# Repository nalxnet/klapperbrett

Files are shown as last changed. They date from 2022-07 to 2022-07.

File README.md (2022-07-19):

# klapperbrett

Die Klappenanzeige (Salzkotten EC2000-FP6) stammt aus einer Zapfsäule und zeigte die üblichen Werte (Literpreis, Gesamtmenge, Gesamtpreis) an.

Es sind drei Anschlüsse vorhanden:
* Pfostenstecker 10-polig, von außen zugänglich: vmtl. Anschluss an den Rest der Zapfsäule, inkl. Stromversorgung (2 Pins +24V, 2 Pins GND).
* Pfostenstecker 12-polig(?), nur von innen zugänglich: vmtl. Service-Anschluss zur Neuprogrammierung, kein +24V oder +5V, nur GND.
* 2 Bohrungen für +24V und GND, nicht verlötet.

Steuerung erfolgt original über einen 8-bit Mikrocontroller, der in einen 40-pol. IC-Sockel gesteckt ist. Hier setzen wir an und ersetzen diesen mit einem Arduino/ESP.

Es gibt 3 Zeilen, die oberen beiden haben 5 Elemente, die unterste hat 4. Jedes Element hat 7 Segmente zur Anzeige einer Zahl. Logisch sind zur Ansteuerung alle Elemente in einer Reihe aufgebaut, dadurch lassen sich die einzelnen Segmente als Matrix darstellen, wobei die Elemente die Spalten und die Segmente die Zeilen darstellen. Jedes Segment besteht aus einem Elektromagneten, der je nach Stromfluss anders polarisiert ist und dadurch das Segment in An- bzw. Aus-Position bewegt. Dafür ist eine Seite der Spule direkt an die Spaltenleitung angeschlossen. Die andere Seite der Spule ist mit jeweils einer Diode an zwei Elementleitungen angeschlossen. Eine zum Bewegen in An-Position, die andere für die Aus-Position.

Die Ansteuerung der einzelnen Segmente übernehmen zwei FP2800A. Der obere (FPZ) steuert die Zeilen, der untere (FPS) die Spalten.

Pinbelegung Mikrocontroller (alle nicht aufgeführten sind unbekannt):
```
1: FPS A0
2: FPS A1
3: FPS A2
4: FPS B0
5: FPS B1
6: (über JP1 an PCF8582C-2 Pin SDA --> I2C)
7: FPS ENABLE
...
20: GND
33: FPZ ENABLE
34: FPZ B0, FPZ DATA, FPS DATA
35: FPZ B1
...
37: FPZ A2
38: FPZ A1
39: FPZ A0
40: +5V
```

Ansteuerung der Segmente erfolgt durch Setzen der Spalten- und Zeilenadresse (je 8 Bit), DATA wird durch invertierenden Schmitt-Trigger bereits passend gesetzt. Um das Segment zu schalten muss abschließend ein kurzer Puls an beiden ENABLE-Pins gleichzeitig (HIGH nach LOW) erfolgen, für dessen Zeit die Spalten- und Zeilenleitung tatsächlich gesetzt wird.

Adressierung der Elemente erfolgt von oben nach unten, von rechts nach links. Freie Element-Plätze sind ebenfalls adressiert, 8 und 16 werden übersprungen.

```
 6  5  4  3  2  1

13 12 11 10  9  7

   19 18 17 15 14
```

Die Adressierung der Segmente erfolgt gegen den Uhrzeigersinn, beginnend mit dem obersten Segment und endend mit dem mittleren Segment. 1-7 schalten das Segment aktiv, 9-15 schalten das Segment inaktiv.

Netzteil 24V, mind. 200mA
 
Pinbelegung X5? (extern)
```
...
2: +24V
3: +24V
...
5: GND
...
9: GND
...
```
 
Pinbelegung X6
 
```
... 
14: GND
15: GND
...
```
 
Pinbelegung X7
 
```
1: +24V
2: GND
```

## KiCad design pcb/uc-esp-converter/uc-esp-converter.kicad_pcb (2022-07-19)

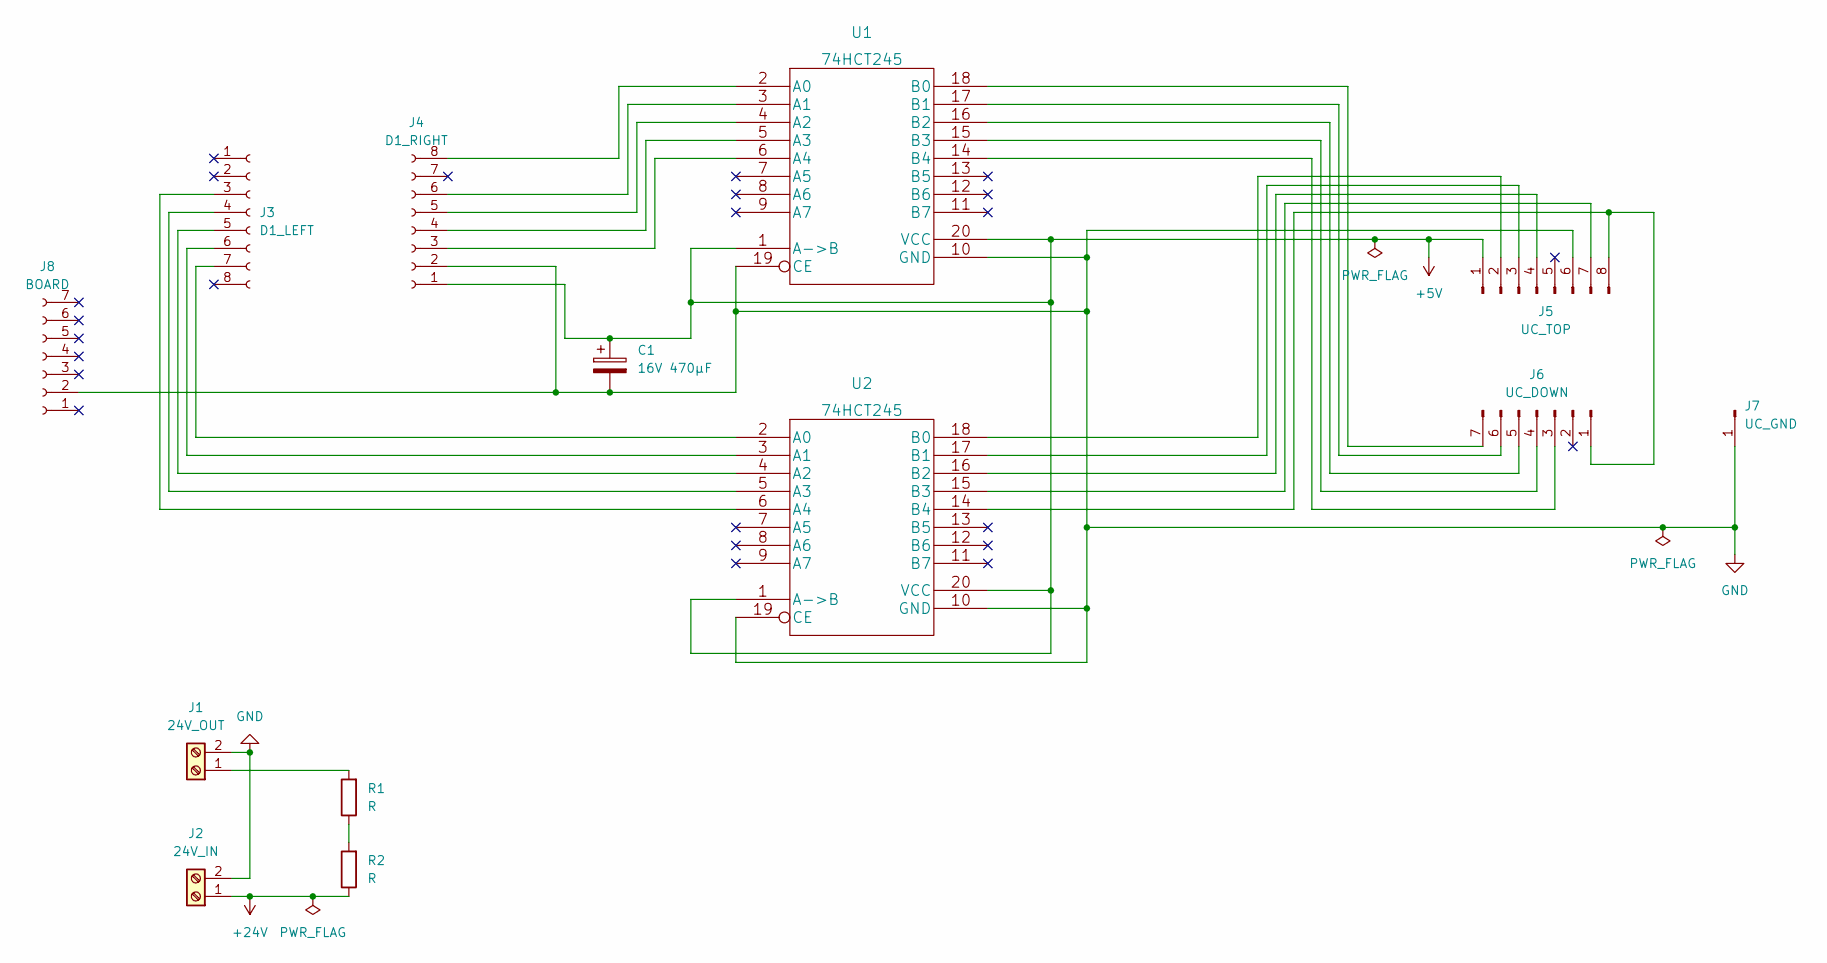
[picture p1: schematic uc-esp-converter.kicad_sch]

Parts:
C1: 16V 470µF; CP_Radial_D10.0mm_P5.00mm
J1: 24V_OUT; TerminalBlock_MetzConnect_Type101_RT01602HBWC_1x02_P5.08mm_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
J2: 24V_IN; TerminalBlock_MetzConnect_Type101_RT01602HBWC_1x02_P5.08mm_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
J3: D1_LEFT; PinSocket_1x08_P2.54mm_Vertical
J4: D1_RIGHT; PinSocket_1x08_P2.54mm_Vertical
J5: UC_TOP; PinHeader_1x08_P2.54mm_Vertical
J6: UC_DOWN; PinHeader_1x07_P2.54mm_Vertical
J7: UC_GND; PinHeader_1x01_P2.54mm_Vertical
J8: BOARD; PinSocket_1x07_P2.54mm_Vertical
R1, R2: R; R_Axial_DIN0207_L6.3mm_D2.5mm_P10.16mm_Horizontal
U1, U2: 74HCT245; DIP-20_W7.62mm

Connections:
+5V: C1.1, J4.1, J5.1, U1.1 (A->B), U1.20 (VCC), U2.1 (A->B), U2.20 (VCC)
+24V: J2.1, R2.1
GND: C1.2, J1.2, J2.2, J4.2, J5.6, J7.1, J8.2, U1.10 (GND), U1.19 (CE), U2.10 (GND), U2.19 (CE)
unnamed: J1.1, R1.2
unnamed: J5.2, U2.18 (B0)
unnamed: J5.3, U2.17 (B1)
unnamed: J5.4, U2.16 (B2)
unnamed: J5.7, U2.15 (B3)
unnamed: J5.8, J6.1, U2.14 (B4)
unnamed: R1.1, R2.2
unnamed: J4.8, U1.2 (A0)
unnamed: J4.6, U1.3 (A1)
unnamed: J4.5, U1.4 (A2)
unnamed: J4.4, U1.5 (A3)
unnamed: J4.3, U1.6 (A4)
unnamed: J6.3, U1.14 (B4)
unnamed: J6.4, U1.15 (B3)
unnamed: J6.5, U1.16 (B2)
unnamed: J6.6, U1.17 (B1)
unnamed: J6.7, U1.18 (B0)
unnamed: J3.7, U2.2 (A0)
unnamed: J3.6, U2.3 (A1)
unnamed: J3.5, U2.4 (A2)
unnamed: J3.4, U2.5 (A3)
unnamed: J3.3, U2.6 (A4)

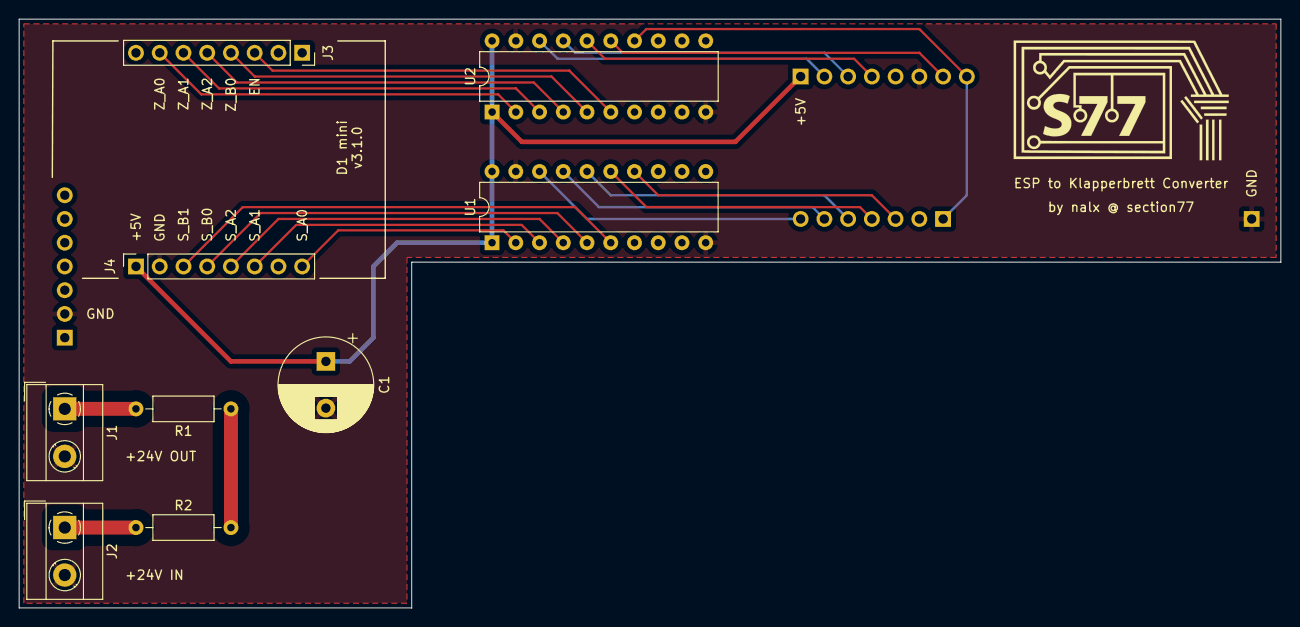
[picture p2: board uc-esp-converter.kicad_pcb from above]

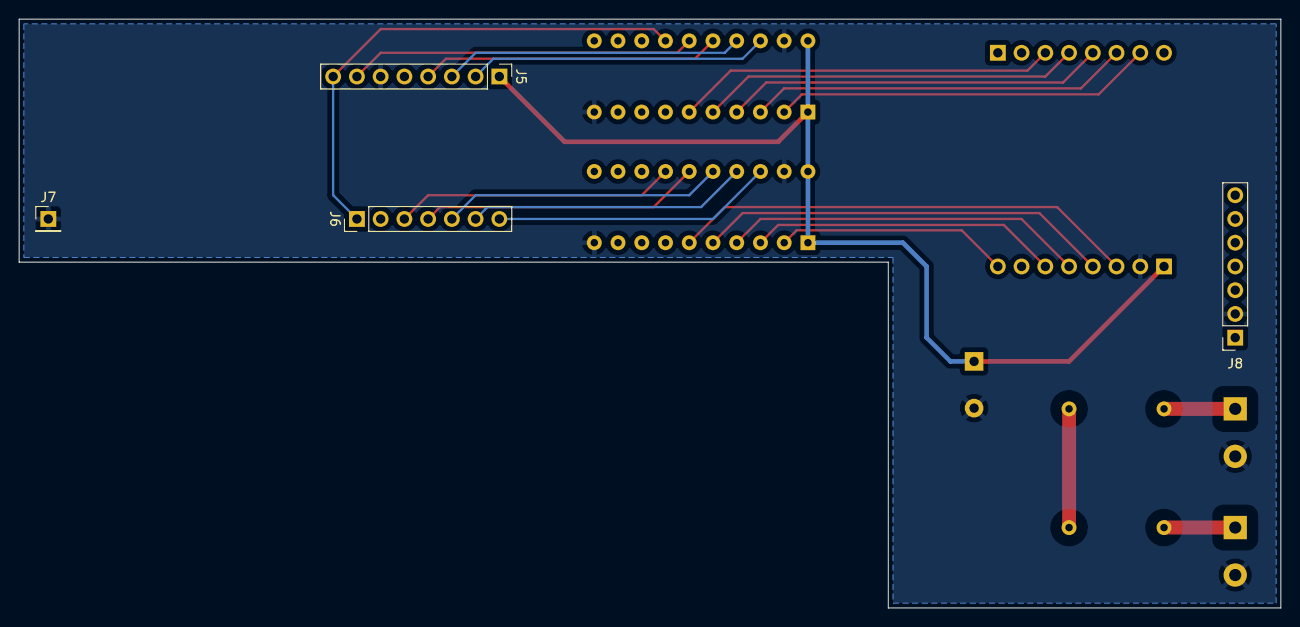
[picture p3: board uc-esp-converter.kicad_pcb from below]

Board: 2 copper layers, 135.0 x 63.0 mm, 14 parts (4 on the bottom side), 25 nets.

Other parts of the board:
Ref**: Val**; section77_logo_kicad

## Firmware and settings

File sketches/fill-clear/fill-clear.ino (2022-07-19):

// Definition der Anschlüsse
// FP2800A unten: Spalte/Element
const int FP_SPALTE_A0 = 1; // TX, GPIO1
const int FP_SPALTE_A1 = D1;
const int FP_SPALTE_A2 = D2;
const int FP_SPALTE_B0 = D3;
const int FP_SPALTE_B1 = D4; // BUILTIN_LED
// FP2800A oben: Zeile/Segment
const int FP_ZEILE_A0 = D8;
const int FP_ZEILE_A1 = D7;
const int FP_ZEILE_A2 = D6;
const int FP_ZEILE_B0 = D5;
const int FP_ENABLE = D0;

// Zeile/Segment wird nur mit 3 Bit addressiert, Bit 4 steuert SET/UNSET und 5 wird nicht verwendet
const int ZEILE_ADDR[3] =  { FP_ZEILE_A0, FP_ZEILE_A1, FP_ZEILE_A2 };
const int SPALTE_ADDR[5] = { FP_SPALTE_A0, FP_SPALTE_A1, FP_SPALTE_A2, FP_SPALTE_B0, FP_SPALTE_B1};

// Zahlen
const boolean ZAHLEN[10][7] = { { true,  true,  true,  true,  true,  true, false},   // 0
                                {false, false, false, false,  true,  true, false},   // 1
                                { true, false,  true,  true, false,  true,  true},   // 2
                                { true, false, false,  true,  true,  true,  true},   // 3
                                {false,  true, false, false,  true,  true,  true},   // 4
                                { true,  true, false,  true,  true, false,  true},   // 5
                                { true,  true,  true,  true,  true, false,  true},   // 6
                                { true, false, false, false,  true,  true, false},   // 7
                                { true,  true,  true,  true,  true,  true,  true},   // 8
                                { true,  true, false,  true,  true,  true,  true} }; // 9

// Buchstaben
const boolean CHARS[26][7] = { { true,  true,  true, false,  true,  true,  true},   // A
                               {false,  true,  true,  true,  true, false,  true},   // b
                               { true,  true,  true,  true, false, false, false},   // C
                               {false, false,  true,  true,  true,  true,  true},   // d
                               { true,  true,  true,  true, false, false,  true},   // E
                               { true,  true,  true, false, false, false,  true},   // F
                               { true,  true, false,  true,  true,  true,  true},   // g (identisch mit 9)
                               {false,  true,  true, false,  true,  true,  true},   // H
                               {false,  true,  true, false, false, false, false},   // I
                               { true, false,  true,  true,  true,  true, false},   // J
                               {false, false, false, false, false, false, false},   // blank, da K nicht darstellbar
                               {false,  true,  true,  true, false, false, false},   // L
                               {false, false, false, false, false, false, false},   // blank, da M nicht darstellbar
                               {false, false,  true, false,  true, false,  true},   // n
                               {false, false,  true,  true,  true, false,  true},   // O
                               { true,  true,  true, false, false,  true,  true},   // P
                               { true,  true, false, false,  true,  true,  true},   // q
                               {false, false,  true, false, false, false,  true},   // r
                               { true,  true, false,  true,  true, false,  true},   // S (identisch mit 5)
                               {false,  true,  true,  true, false, false,  true},   // t
                               {false,  true,  true,  true,  true,  true, false},   // U
                               {false, false, false, false, false, false, false},   // blank, da V nicht darstellbar
                               {false, false, false, false, false, false, false},   // blank, da W nicht darstellbar
                               {false, false, false, false, false, false, false},   // blank, da X nicht darstellbar
                               {false, false, false, false, false, false, false},   // blank, da Y nicht darstellbar
                               { true, false,  true,  true, false,  true,  true} }; // Z (identisch mit 2)
const boolean DASH[7] = {false, false, false, false, false, false, true};
const boolean UNDERSCORE[7] = {false, false, false, true, false, false, false};
const boolean DEGREE[7] = {true, true, false, false, false, true, true};
const boolean EQUALS[7] = {false, false, false, true, false, false, true};
const boolean DOUBLEQUOTE[7] = {false, true, false, false, false, true, false};
const boolean SINGLEQUOTE[7] = {false, true, false, false, false, false, false};
const boolean BRACKET_OPEN[7] = {true, true, true, true, false, false, false};
const boolean BRACKET_CLOSE[7] = {true, false, false, true, true, true, false};
const boolean MUE[7] = {false, true, true, false, false, true, true};

// Zustände der Segmente
const boolean checkState = true;
boolean state[18][7];

// TODO Optimierung
// * Das mittlere Segment flipt an manchen Stellen nur unzuverlässig zurück. Scheint nicht an der Pulslänge oder dem Abstand des Pulses zu liegen. Mechanischer Verschleiß?
// * Globale Variablen für Pin-Adressen auf byte umstellen?
// * Arrays um ungenutzte Zeilen reduzieren und Adressierung entsprechend umstellen

// TODO Features
// * Funktion, die beliebig langen String in einer Zeile schreibt. Wenn String länger als Zeile muss dieser durchlaufen.

void setup() {
  pinMode(FP_SPALTE_B1, FUNCTION_3); // Alternativer Modus für TX: GPIO1
  
  // Alle Pins als OUTPUT setzen
  pinMode(FP_SPALTE_A0, OUTPUT);
  pinMode(FP_SPALTE_A1, OUTPUT);
  pinMode(FP_SPALTE_A2, OUTPUT);
  pinMode(FP_SPALTE_B0, OUTPUT);
  pinMode(FP_SPALTE_B1, OUTPUT);
  pinMode(FP_ZEILE_A0, OUTPUT);
  pinMode(FP_ZEILE_A1, OUTPUT);
  pinMode(FP_ZEILE_A2, OUTPUT);
  pinMode(FP_ZEILE_B0, OUTPUT);
  pinMode(FP_ENABLE, OUTPUT);

  // ENABLE muss auf HIGH gehalten werden und darf nur für kurze Pulse auf LOW gesetzt werden!
  digitalWrite(FP_ENABLE, HIGH);

  // Adressen auf HIGH initialisieren
  digitalWrite(FP_SPALTE_A0, HIGH);
  digitalWrite(FP_SPALTE_A1, HIGH);
  digitalWrite(FP_SPALTE_A2, HIGH);
  digitalWrite(FP_SPALTE_B0, HIGH);
  digitalWrite(FP_SPALTE_B1, LOW);
  digitalWrite(FP_ZEILE_A0, HIGH);
  digitalWrite(FP_ZEILE_A1, HIGH);
  digitalWrite(FP_ZEILE_A2, HIGH);
  digitalWrite(FP_ZEILE_B0, HIGH); // LOW=SET, HIGH=UNSET

  delay(2000); // Zeit zum Spannungsaufbau (Kondensator) lassen...

  resetState();
}

void loop() {
  clearAll();

  delay(2000);

  fillAll();

  delay(2000);
}

byte getSpalte(byte idx) {
  if (idx > 13) {
    return 0;
  }
  
  if (idx >= 0 && idx < 5) {
    return 5 - idx;
  }

  if (idx >= 5 && idx < 10) {
    byte spalte = 17 - idx;
    if (spalte % 8 == 0) {
      return spalte - 1;
    } else {
      return spalte;
    }
  }

  if (idx < 12) {
    return 28 - idx;
  } else {
    return 27 - idx;
  }
  
}

void writeNoWiFi() {
  writeChar(5,'n');
  writeChar(4,'o');
  writeChar(3,' ');
  writeChar(2,' ');
  writeChar(1,' ');
  writeChar(12,'n');
  writeChar(11,'e');
  writeChar(10,'t');
  writeChar(9,' ');
  writeChar(7,' ');
  writeChar(18,'c');
  writeChar(17,'o');
  writeChar(15,'n');
  writeChar(14,'n');
}

void writeDisconnect() {
  writeChar(5,'n');
  writeChar(4,'o');
  writeChar(3,' ');
  writeChar(2,' ');
  writeChar(1,' ');
  writeChar(12,'s');
  writeChar(11,'e');
  writeChar(10,'r');
  writeChar(9,' ');
  writeChar(7,' ');
  writeChar(18,'c');
  writeChar(17,'o');
  writeChar(15,'n');
  writeChar(14,'n');
}

void writeVersion() {
  writeChar(5,'s');
  writeChar(4,'u');
  writeChar(3,'b');
  writeChar(2,'c');
  writeChar(1,'l');
  writeChar(12,'i');
  writeChar(11,'e');
  writeChar(10,'n');
  writeChar(9,'t');

  writeChar(18,'r');
  writeChar(17,'0');
  writeChar(15,'0');
  writeChar(14,'3');
}

void writeSection77() {
  writeChar(5,'S');
  writeChar(4,'E');
  writeChar(3,'C');
  writeChar(12,'t');
  writeChar(11,'i');
  writeChar(10,'o');
  writeChar(9,'n');

  for (int i = 0; i < 78; i++) {
    byte links = i / 10;
    byte rechts = i % 10;
    writeNumber(18, links);
    writeNumber(17, rechts);
    delay(5);
  }
}

// ----------------------------------------------------------------------
// Lib-Funktionen
// ----------------------------------------------------------------------

void writeString(String s) {
  for (int i = 0; i < s.length(); i++) {
    writeChar(getSpalte(i), s.charAt(i));
  }
}

void writeDegree(byte spalte) {
  for (int i = 0; i < 7; i++) {
    writeAt(spalte, i+1, DEGREE[i]);
  }
}

void writeMue(byte spalte) {
  for (int i = 0; i < 7; i++) {
    writeAt(spalte, i+1, MUE[i]);
  }
}

void writeChar(byte spalte, char c) {
  int number = c - '0';
  if (number >= 0 && number <= 9) {
    writeNumber(spalte, number);
    return;
  }
  
  if (c == '-') {
    for (int i = 0; i < 7; i++) {
      writeAt(spalte, i+1, DASH[i]);
    }
    return;
  }

  if (c == '_') {
    for (int i = 0; i < 7; i++) {
      writeAt(spalte, i+1, UNDERSCORE[i]);
    }
    return;
  }

  if (c == '=') {
    for (int i = 0; i < 7; i++) {
      writeAt(spalte, i+1, EQUALS[i]);
    }
    return;
  }

  if (c == '"') {
    for (int i = 0; i < 7; i++) {
      writeAt(spalte, i+1, DOUBLEQUOTE[i]);
    }
    return;
  }

  if (c == '\'' || c == '`') {
    for (int i = 0; i < 7; i++) {
      writeAt(spalte, i+1, SINGLEQUOTE[i]);
    }
    return;
  }

  if (c == '[' || c == '(' || c == '{') {
    for (int i = 0; i < 7; i++) {
      writeAt(spalte, i+1, BRACKET_OPEN[i]);
    }
    return;
  }

  if (c == ']' || c == ')' || c == '}') {
    for (int i = 0; i < 7; i++) {
      writeAt(spalte, i+1, BRACKET_CLOSE[i]);
    }
    return;
  }
  
  byte charArrayPos = getPosInAlphabet(c);
  if (charArrayPos >= 0 && charArrayPos < 26) {
    for (int i = 0; i < 7; i++) {
      writeAt(spalte, i+1, CHARS[charArrayPos][i]);
    }
  } else {
    clearAt(spalte);
  }
}

void writeNumber(byte spalte, byte number) {
  byte mod = number % 10;
  for (int i = 0; i < 7; i++) {
    writeAt(spalte, i+1, ZAHLEN[mod][i]);
  }
}

void clearAt(byte spalte) {
  for (int i = 1; i < 8; i++) {
    writeAt(spalte, i, false);
  }
}

void fillAt(byte spalte) {
  for (int i = 1; i < 8; i++) {
    writeAt(spalte, i, true);
  }
}

void clearAll() {
  writeAll(false);
}

void fillAll() {
  writeAll(true);
}

// ----------------------------------------------------------------------
// Hilfsfunktionen
// ----------------------------------------------------------------------

byte getPosInAlphabet(char c) {
  return tolower(c) - 'a';
}

void resetState() {
  for (int i = 1; i < 19; i++) {
    if (i == 6 || i == 8 || i == 13 || i == 16) {
      // Unbelegte Spaltenadressen
      continue;
    }
    for (int j = 1; j < 8; j++) {
      writeAtStateless(i, j, false);
    }
  }
}

void writeAll(boolean set) {
  for (int i = 1; i < 19; i++) {
    if (i == 6 || i == 8 || i == 13 || i == 16) {
      // Unbelegte Spaltenadressen
      continue;
    }
    writeAllSegments(i, set);
  }
}

void writeAllSegments(byte spalte, boolean set) {
  for (int i = 1; i < 8; i++) {
    writeAt(spalte, i, set);
  }
}

void writeAt(byte spalte, byte zeile, boolean set) {
  if (!checkState || state[spalte-1][zeile-1] != set) {
    writeAtStateless(spalte, zeile, set);
  }
}

void writeAtStateless(byte spalte, byte zeile, boolean set) {
  for (int i = 0; i < 5; i++) {
    boolean isSet = bitRead(spalte, i);
    if (isSet) {
      digitalWrite(SPALTE_ADDR[i], HIGH);
    } else {
      digitalWrite(SPALTE_ADDR[i], LOW);
    }
  }

  for (int i = 0; i < 3; i++) {
    boolean isSet = bitRead(zeile, i);
    if (isSet) {
      digitalWrite(ZEILE_ADDR[i], HIGH);
    } else {state[spalte-1][zeile-1] = set;state[spalte-1][zeile-1] = set;
      digitalWrite(ZEILE_ADDR[i], LOW);
    }
  }

  if (set) {
    digitalWrite(FP_ZEILE_B0, LOW);
  } else {
    digitalWrite(FP_ZEILE_B0, HIGH);
  }

  fire();
  state[spalte-1][zeile-1] = set;
}

void fire() {
  digitalWrite(FP_ENABLE, LOW);
  delay(1);
  digitalWrite(FP_ENABLE, HIGH);
  delay(1);

  // Adresse zurücksetzen
  // TODO Notwendig? ggf. entfernen...
  digitalWrite(FP_SPALTE_A0, HIGH);
  digitalWrite(FP_SPALTE_A1, HIGH);
  digitalWrite(FP_SPALTE_A2, HIGH);
  digitalWrite(FP_SPALTE_B0, HIGH);
  digitalWrite(FP_SPALTE_B1, LOW);
  digitalWrite(FP_ZEILE_A0, HIGH);
  digitalWrite(FP_ZEILE_A1, HIGH);
  digitalWrite(FP_ZEILE_A2, HIGH);
  digitalWrite(FP_ZEILE_B0, HIGH);
}

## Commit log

2022-07-19 update pin assignments to pcb layout
2022-07-19 add pcb files
    [uc-esp-converter.kicad_pcb, uc-esp-converter.kicad_sch]
2022-07-19 update readme with device documentation
